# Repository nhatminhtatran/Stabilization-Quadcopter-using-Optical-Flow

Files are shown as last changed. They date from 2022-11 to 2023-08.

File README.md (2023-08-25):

<p align="center">
 <h1 align="center">Project on Robotics - Design model and PID controller for balanced Quadcopter using Optical Flow algorithm</h1>
</p>

# Introduction
This project does the following tasks:
- Build hardware for Quadcopter model with dimensions 198x235x85 mm.
- Design a PID controller to stabilize the position of the Quadcopter chassis.
- Use Optical Flow image processing to keep Quadcopter balance.
- Conduct actual operation to check the response of the controller.

# Design Quadcopter model
Quadcopter is a UAV with 4 propeller engines, which generate lift for the aircraft to take off. The direction of the quadcopter propeller along with the rotation and speed are factors that determine the aircraft's ability to fly and maneuver.

Quadcopter is a robot with 6 degrees of freedom. Therefore, in addition to translational motions in the x, y and z directions, it also moves in the roll, pitch and yaw angles.

<p align="center">
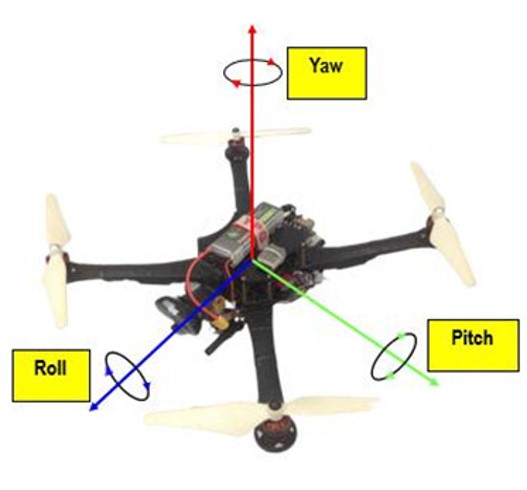
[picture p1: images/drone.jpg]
  <br/>
  <i>Movement structure of Quadcopter</i>
</p>

The model of the Quadcopter in practice after construction is as follows:

<p align="center">
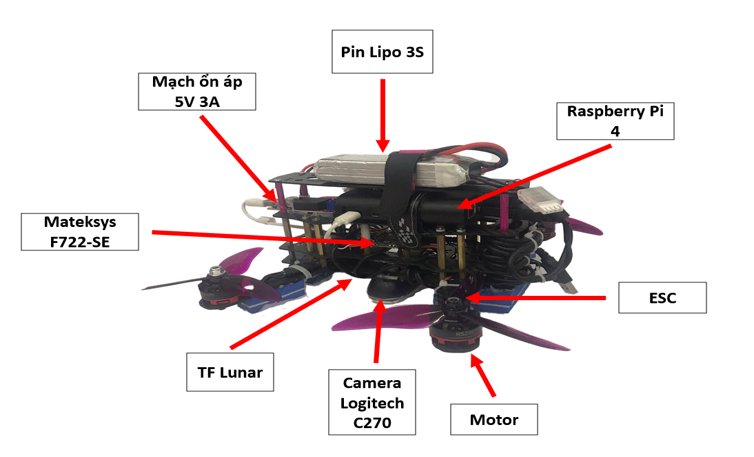
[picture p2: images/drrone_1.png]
  <br/>
  <i>Quadcopter hardware overview</i>
</p>

In this project, we use Camera Logitech C270 to apply Optical Flow to calculate drift from the Center of Frame and TF-Lunar 1D Lidar to calculate height of the Quadcopter. After that, we use that two-signal to control Quadcopter through two PID-controller. The protocol we use to control Quadcopter is YAMSPy (Yet Another Multiwii protocol).

# Optical Flow algorithm
The image processing algorithm used in the project is presented as the flowchart below:

<p align="center">
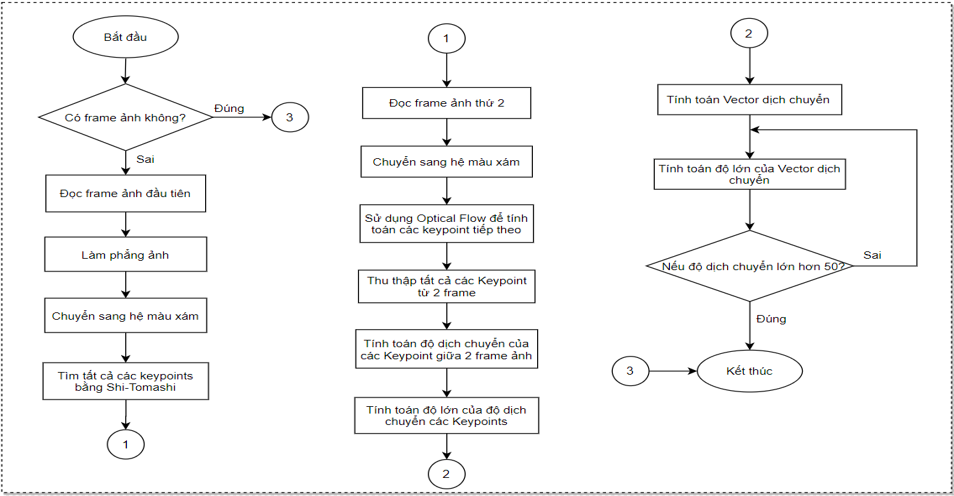
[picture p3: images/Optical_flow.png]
  <br/>
  <i>Flowchart of image processing algorithm</i>
</p>

The above diagram shows the whole process of finding the displacement vector to generate the input value for balancing. First, the camera will read the first image frame, then flatten the image from the parameters after the camera Calibration because the image retrieved from the camera will be curved so the displacement vector will be incorrect. Then convert the image frame to grayscale. Because after flattening the image, the edge of the image will appear as a cut angle, making the Harris Corner algorithm recognize it as a keypoint, which will cause errors in the vector calculation. That's why we have to cut the center part. Then, using Harris Corner algorithm to find keypoints in the image frames. Then use Optical flow algorithm to calculate the displacement between frames and get the corresponding Displacement Vector value.

<p align="center">
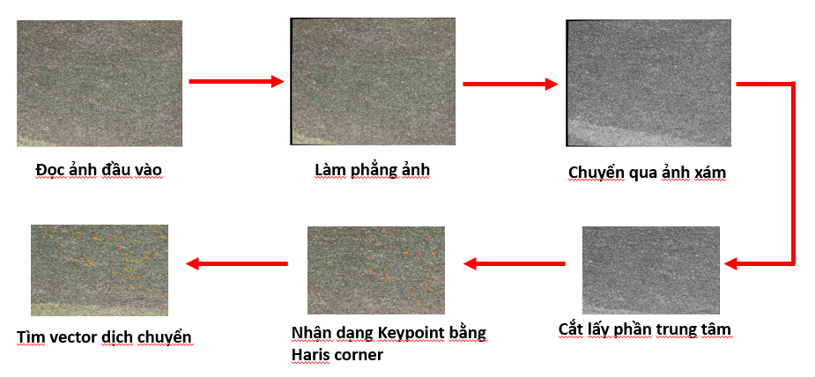
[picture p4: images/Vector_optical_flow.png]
  <br/>
  <i>Displacement Vector Calculation Process</i>
</p>

However, there are still cases that cause the process to be terminated. That is when the Quadcopter moves too far from the original point (50cm), the image processing algorithm will end. Then, Quadcopter will update the Keypoints and start the image processing again.

# Build a PID controller
The first controller is the altitude controller. In order for the Quadcopter to maintain altitude, the control signal value is the Throttle control pulse output value. In order for the Quadcopter to maintain the desired altitude, the PID controller value needs to be calibrated so that the Throttle value is calculated around the equilibrium working point.

<p align="center">
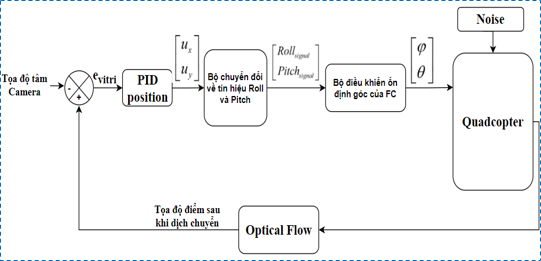
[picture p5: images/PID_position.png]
  <br/>
  <i>Block diagram of position PID controller</i>
</p>

<p align="center">
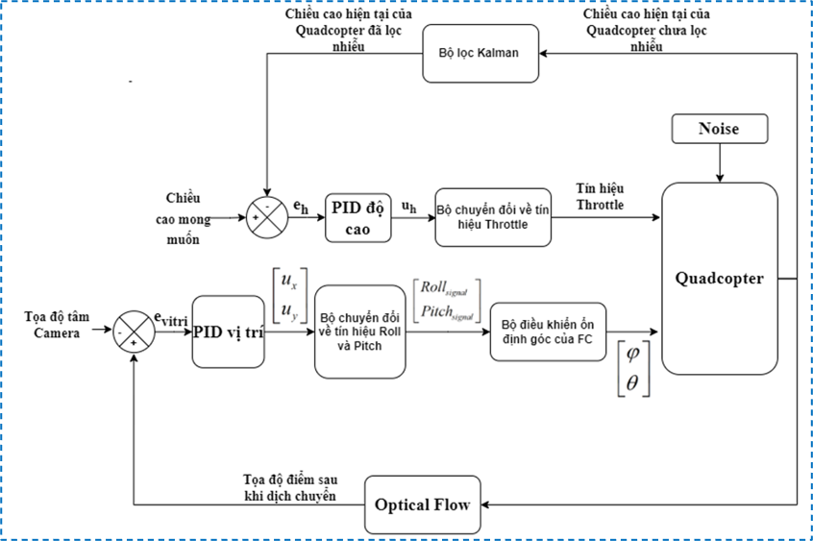
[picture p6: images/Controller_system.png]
  <br/>
  <i>General controller of the system</i>
</p>

# Results and reviews

- **Evaluation of image processing algorithms:**
Because the camera is always curved, the value of the image processing algorithm is often wrong. Therefore, the process of camera calibration plays a very important role.
<p align="center">
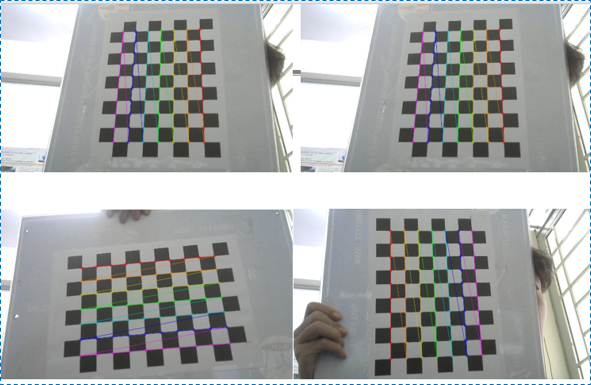
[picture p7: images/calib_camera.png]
  <br/>
  <i>Camera calibration process</i>
</p>

- **Optical Flow algorithm results:**
Result of applying PLK (Pyramid Lucas – Kanade) algorithm when there are few features (left figure).
Result of applying PLK (Pyramid Lucas – Kanade) algorithm when there are many features (right figure).

<div style="display: flex;">
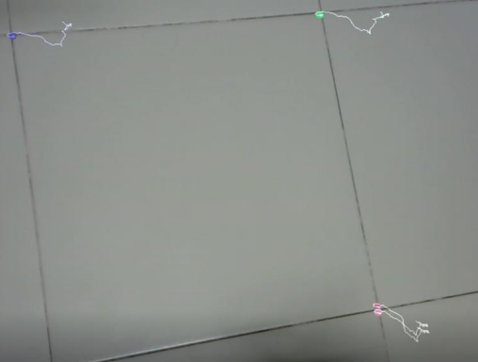
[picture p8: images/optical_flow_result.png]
  
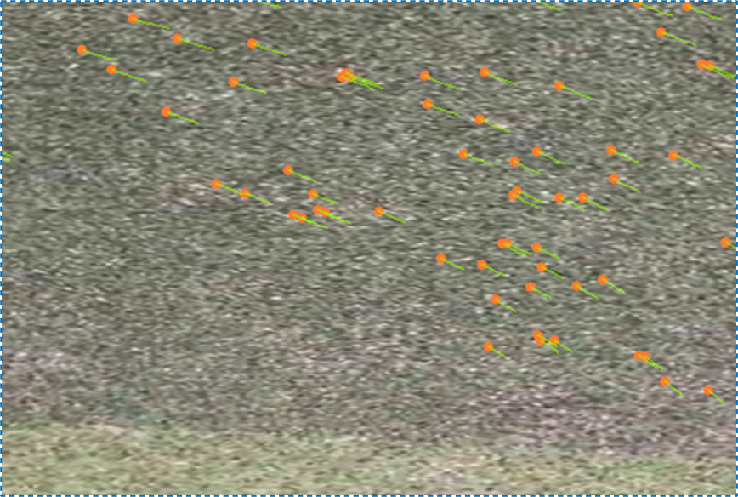
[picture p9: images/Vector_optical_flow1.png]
  
</div>

- **Evaluation of the PID controller:**
The PID controller applies to the Drone model to control altitude and position hold.

<p align="center">
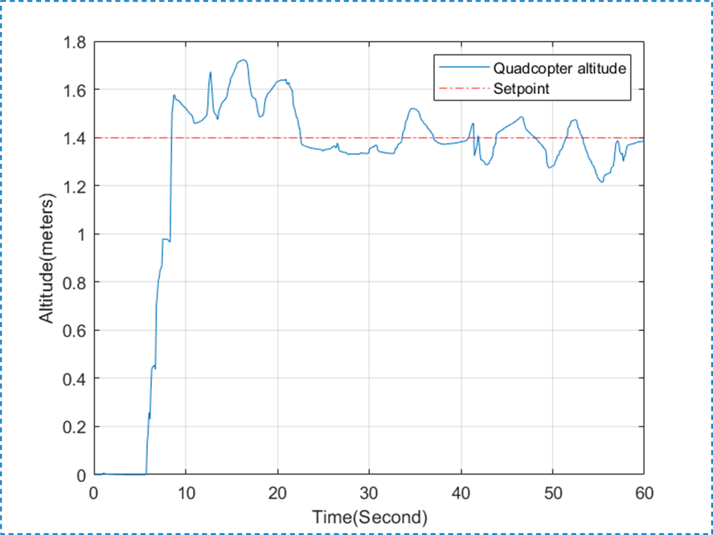
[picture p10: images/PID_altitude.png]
  <br/>
  <i>Result of PID controller holding altitude</i>
</p>

<p align="center">
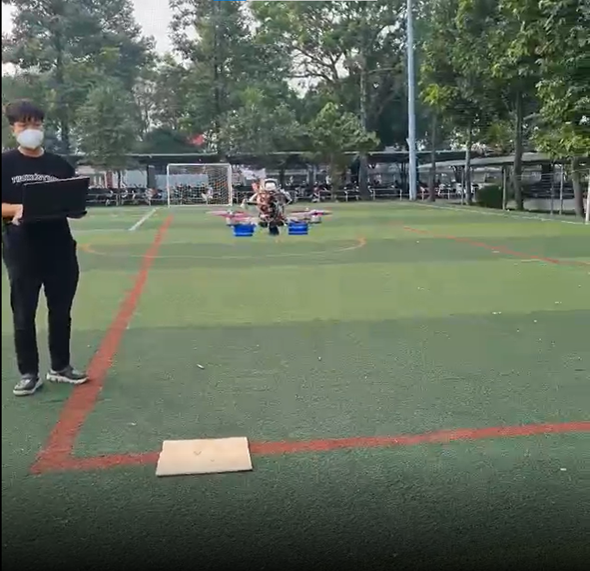
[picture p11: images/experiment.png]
  <br/>
  <i>Realistic results quadcopter keeps altitude and position</i>
</p>

# Video
https://youtu.be/sdybXYhyMzA

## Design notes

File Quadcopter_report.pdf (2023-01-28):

## BỘ GIÁO DỤC & ĐÀO TẠO

### TRƯỜNG ĐẠI HỌC SƯ PHẠM KỸ THUẬT TP. HỒ CHÍ MINH

### KHOA ĐIỆN – ĐIỆN TỬ

### BỘ MÔN TỰ ĐỘNG ĐIỀU KHIỂN

-----------------⸙∆⸙-----------------

# ĐỒ ÁN MÔN HỌC

## ĐỀ TÀI:Thiết kế mô hình và bộ điều khiển PID cho

## Quadcopter cân bằng dùng thuật toán Optical Flow

### Tp. Hồ Chí Minh tháng 1 năm 2023

### GVHD: TS. Trần Đức Thiện

SVTH: | MSSV:
Nguyễn Đức Mạnh | 19151253
Tạ Trần Nhật Minh | 19151034

## Hình ảnh đề tài

## Lời cảm ơn

Trong khoảng thời gian ba năm được học tập và rèn luyện dưới mái trường Đại học Sư phạm Kỹ thuật Tp. Hồ Chí Minh đã cho chúng em cơ hội tiếp thu những kiến

thức không chỉ có trong sách vở mà còn là những câu chuyện thực tế, những ví dụ minh

họa sinh động được các Thầy, Cô truyền đạt vào những buổi học lý thuyết và thực hành,

tất cả sẽ là hành trang tri thức quý báu, là nền tảng vững vàng nâng bước chúng em trên

con đường sự nghiệp phía trước.
Nhóm em xin được gửi lời cảm ơn chân thành đến thầy TS. Trần Đức Thiện đã tận

tình chỉ bảo, hướng dẫn và đóng góp những ý kiến vô cùng quý giá giúp nhóm em hoàn

thành đồ án môn học này. Nhóm cũng xin cám ơn quý Thầy, Cô đang công tác tại khoa

Điện - Điện tử cùng các Thầy, Cô trong toàn trường đã giảng dạy nhiệt tình và truyền

tải các kinh nghiệm quý giá cho nhóm trong suốt ba năm học vừa qua.

Tuy đã có sự chuẩn bị trong bài báo cáo đồ án môn học này song không thể tránh

khỏi những sai sót. Vì vậy, nhóm em rất mong nhận được sự chỉ bảo, đóng góp ý kiến

của quý Thầy Cô để nhóm có cơ hội nâng cao kiến thức và kĩ năng của mình, cũng như

là một nền tảng vững chắc để nhóm tiến xa hơn trong tương lai.

Nhóm em xin chân thành cảm ơn!

## Mục lục

Mục lục

## Danh sách hình ảnh

## Danh sách bảng

CHƯƠNG 1. TỔNG QUAN

BỘ MÔN ĐIỀU KHIỂN TỰ ĐỘNG | 1

## Chương 1. TỔNG QUAN

### 1.1 GIỚI THIỆU

Trong những năm gần đây, với sự phát triển của công nghệ 4.0, UAV (Unmanned

Arial Vehicle) ngày càng phổ biến và được sử dụng rộng rãi trong nhiều lĩnh vực trong

cuộc sống, từ trong nông nghiệp cho đến quân sự. UAV được định nghĩa là phương tiện

cơ giới không có người lái, sử dụng lực khí động học để di chuyển. UAV có thể bay

thông qua tín hiệu điều khiển bằng tay cầm hoặc tự hành bằng các hệ thống máy tính

nhúng xử lý chương trình điều khiển. Các quốc gia phát triển như Mỹ, Nga, Trung Quốc

đều đang đẩy mạnh phát triển các hệ thống máy bay không người lái vào trong lĩnh vực

quân sự. Ngoài ra, các biến thể của UAV còn được sử dụng rộng rãi trong tìm kiếm cứu

hộ, khai thác những nơi mà con người không thể đặt chân đến được, hay áp dụng trong

việc giao hàng, quay phim...
Quadcopter là một dạng phổ biến nhất của UAV được trang bị với bốn động cơ và

bốn cánh quạt, hoạt động dựa trên nguyên lý động học. Quadcopter bắt đầu định hình

được cấu trúc máy bay vào đầu những năm thập niên 2000s. Mãi cho đến giai đoạn từ

2005-2010, với sự ra đời của nhiều vi điều khiển và cảm biến có kích thước và khối

lượng nhỏ như IMU, Barometer, đã tạo điều kiện cho sự phát triển bùng nổ của

Quadcopter với khả năng giao tiếp đa dạng và dễ dàng thiết kế nhỏ gọn hơn trước. Chính

vì sự đa di năng của các hệ thống quadcopter, ngày nay nhiều thuật toán điều khiển

thông minh như xử lý ảnh hay trí tuệ nhân tạo ngày càng được áp dụng nhiều trên các

mô hình quadcopter này. Do đó tình hình nghiên cứu về drone ngày càng được mở rộng

và phát triển cả trên thị trường quốc tế và trong nước.

### 1.1.1 Nghiên cứu quốc tế

Trong những năm gần đây, thị trường thương mại của drone đang ngày càng phát

triển mạnh mẽ. Mặc dù sự ra đời của Covid-19 đã tác động nghiêm trọng đến nhu cầu

sử dụng và chế tạo máy bay không người lái, việc kết nối lại các hoạt động kinh tế vào

năm 2021 đã phục hồi nhu cầu về máy bay không người lái. Máy bay không người lái

đã định nghĩa lại và nâng cao năng suất của nhiều ngành. Với sự tăng trưởng trong việc

ứng dụng drone trong các lĩnh vực khác nhau, các công ty đang đầu tư đáng kể vào các

CHƯƠNG 1. TỔNG QUAN

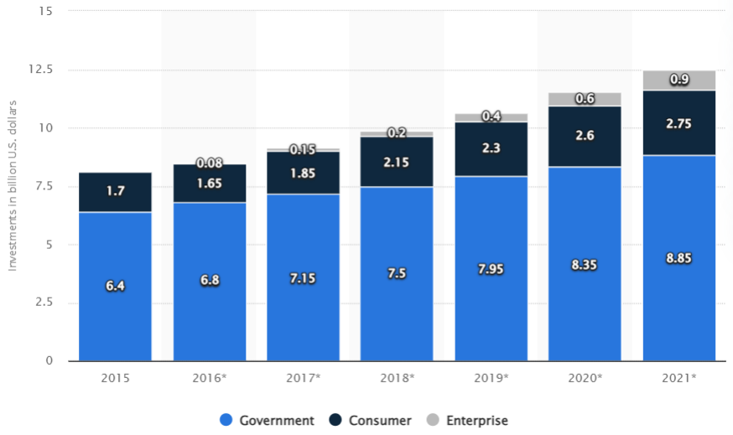
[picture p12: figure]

BỘ MÔN ĐIỀU KHIỂN TỰ ĐỘNG | 2

giải pháp phân tích chế tạo máy bay không người lái. Trong đó DJI là hãng sản suất

drone lớn nhất thế giới có trụ sở tại Trung Quốc và nơi đây đã trở thành trung tâm sản

xuất máy bay không người lái toàn cầu trong sáu năm qua. Hãng nghiên cứu thị trường

BI Intelligence đã đưa ra ước tính đầu tư phần cứng của drone trên thị trường toàn cầu

đạt hơn 12 tỷ USD vào năm 2021.

Hình 1.1: Thị phần đầu tư vào lĩnh vực drone tính đến năm 2021

Hình 1.2: DJI Mavic Pro Mini

Flycam
Flycam là thiết bị bay không người lái được trang bị camera cho phép người dùng

điều khiển, quan sát từ xa để chụp ảnh và ghi hình trên cao. Hiện nay thiết bị này chắc

hẳn không còn xa lạ với mọi người. Flycam ngày càng được đổi mới về kiểu dáng, kích

thước, thời gian bay, khoảng cách điều khiển, chất lượng camera, công nghệ và giá cả

hợp lý. Hình dưới đây cho thấy hình ảnh một chiếc Flycam khá phổ biến trên thị trường

– DJI Mavic 3.

CHƯƠNG 1. TỔNG QUAN

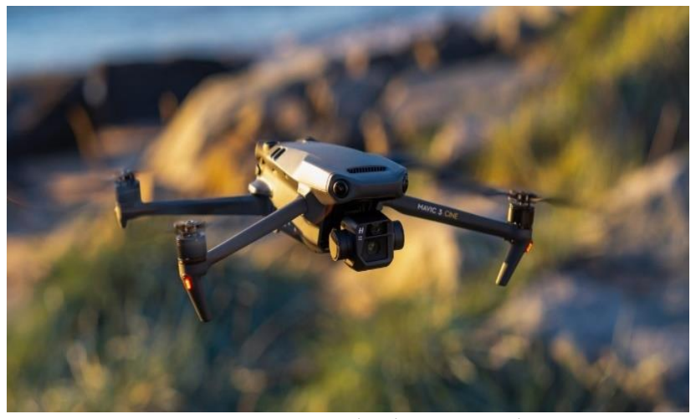
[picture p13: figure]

BỘ MÔN ĐIỀU KHIỂN TỰ ĐỘNG | 3

Hình 1.3: Một mô hình DJI Mavic 3

Drone với công nghệ theo dõi đối tượng và tránh vật cản

Với công nghệ theo dõi đối tượng, drones được lập trình để bay bám theo đối

tượng, mang đến những thước phim độc đáo. Với DJI Mavic3, hãng có sử dụng công

nghệ Active Track, người dùng có thể chọn bounding box bao quanh đối tượng cần

Track và drone sẽ bay bám theo đối tượng đó. Tính năng Follow-me cũng giúp drone

bay theo người khi chỉ có một người trong khung hình bằng cách sử dụng GPS. Bên

cạnh đó, việc trang bị các cảm biến Lidar giúp drone có thể tránh vật cản trong quá trình

bay.

Hình 1.4: Drone bay bám theo đối tượng

Máy bay không người lái sử dụng GPS/GCS
Máy bay không người lái trang bị GPS, được điều khiển từ xa thông qua các thiết

bị như điện thoại, máy tính bảng hoặc máy tính cùng với một máy phát sóng radio telemetry được gọi là trạm điều khiển mặt đất (GCS). Từ trạm điều khiển mặt đất, máy

bay có thể được điều khiển theo một lộ trình được quy hoạch sẵn. Ngoài ra, máy bay

không người lái có thể được lập trình để theo dõi máy phát có trang bị GPS để giữ đối

tượng trong khung hình máy ảnh. Việc theo dõi đối tương sử dụng GPS cũng là một

CHƯƠNG 1. TỔNG QUAN

BỘ MÔN ĐIỀU KHIỂN TỰ ĐỘNG | 4

hướng nghiên cứu và đã có sản phầm thương mại. Tuy nhiên GPS cũng có nhược điểm

là dễ bị nhiễu sóng và mất tín hiệu ở một số nơi địa hình rừng núi hiểm trở.

Drone trình diễn ánh sáng

Drone ngày nay còn được ứng dụng trong các dự án trình diễn ánh sáng cho các

sự kiện lớn. Dự án trình diễn ánh sáng bằng drone đạt kỷ lục Guinness của hãng xe hơi

Genesis Trung Quốc với 3281 drones.

Hình 1.5: Drone trình diễn ánh sáng

### 1.1.2 Nghiên cứu trong nước

Nghiên cứu của sinh viên trong nước
Chủ đề drone là một chủ đề khá hấp dẫn và thu hút nhiều bạn sinh viên đam mê

nghiên cứu. Nhiều mô hình drone đã được chọn để nghiên cứu trong các luận văn đồ án

tốt nghiệp cũng như nghiên cứu khoa học. Tuy nhiên yêu cầu nhiều về kiến thức khoa

học và việc thiếu kinh nghiệm nghiên cứu UAV, nên các đề tài về máy bay không người

lái của sinh viên vẫn còn nhiều hạn chế. Máy bay không người lái kết hợp với các công

nghệ mới như xử lý ảnh, thuật toán AI, IoT,… đã và đang được nghiên cứu và giảng dạy ngày càng nhiều tại các trường đại học.

Tình hình nghiên cứu một số đề tài tiêu biểu về drone của trường đại học Sư Phạm

Kỹ thuật TP.Hồ Chí Minh được trình bày như bảng 1:

CHƯƠNG 1. TỔNG QUAN

BỘ MÔN ĐIỀU KHIỂN TỰ ĐỘNG | 5

Bảng 1: Các đề tài nghiên cứu về drone ở trường đại học Sư phạm Kỹ thuật TP. HCM

STT | Tên đề tài | Tác giả | Khóa | Nội dung
1 | Design and implement a quadcopter model autonomuosly landing on a stationary target | Trần Lê Anh, Lê Tuấn Thông | K14 | Thiết kế và sử dụng các bộ điều khiển PID, LQR, bộ lọc Kalman và giải thuật xử lý ảnh để quadcopter tự động hạ cánh trên một vị trí xác định.
2 | Research, design and construct an autonomuos human detection and tracking quadcopter prototype | Lê Mạnh Cường | K15 | Nghiên cứu, thiết kế và ứng dụng bộ điều khiển PID, mạng học sâu SSD MobileNet v2-lite và thuật toán tracking để quadcopter tự động phát hiện và bám theo người.
3 | Xây dựng mô hình quadcopter và điều khiển bay bám theo đối tượng | Nguyễn Văn Minh Phụng, Nguyễn Thành Quang | K16 | Nghiên cứu, thiết kế và ứng dụng bộ điều khiển PID và giải thuật xử lý ảnh để drone bay bám theo một vật thể di động.
4 | Nghiên cứu, thiết kế và chế tạo mô hình quadcopter tự hành bay qua khoảng trống hẹp | Lê Ngọc Hiền Đức | K17 | Nghiên cứu, thiết kế và chế tạo mô hình quadcopter; sử dụng giải thuật xử lý ảnh và tính toán quỹ đạo để quadcopter bay qua một khoảng trống hẹp.
5 | Điều khiển mô hình drone bay bám theo đối tượng | Trương Lê Anh Tiến | K18 | Nghiên cứu, áp dụng giải thuật thị giác máy và mô hình mạng học sâu để điều khiển drone bay bám theo đối tượng.

Nghiên cứu máy bay không người lái
Về lĩnh vực này nước ta cũng đạt được một số thành tựu nhất định. Có nhiều trung

tâm, công ty nghiên cứu về UAV đã đạt được nhiều kết quả rất khả quan. Các mô hình

đã đáp ứng được nhu cầu thực tế được đặt ra, đáp ứng được yêu cầu trong nước lẫn quốc

tế. Đi đầu trong lĩnh vực này là các trung tâm nghiên cứu của Bộ quốc phòng với nhiều

loại máy bay không người lái thực hiện các nhiệm vụ quân sự, nghiên cứu, giám sát trên không và cứu hộ cứu nạn. Bên cạnh đó cũng có nhiều công ty sản xuất và cung cấp giải

pháp về drone, ứng dụng chủ yếu trong các lĩnh vực nông nghiệp, công nghiệp và đã

xuất khẩu sang các thị trường Mỹ, Châu Âu, Ấn Độ, …. Hình dưới đây là mô hình

CHƯƠNG 1. TỔNG QUAN

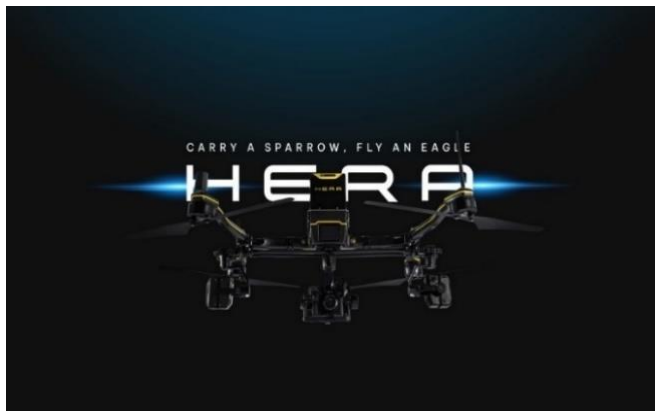
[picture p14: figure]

BỘ MÔN ĐIỀU KHIỂN TỰ ĐỘNG | 6

HERA Drone mới nhất của Công ty TNHH Real-time Robotics Việt Nam được đem đi

triển lãm tại Mỹ, là niềm tự hào của ngành công nghiệp Drone Việt Nam.

Hình 1.6: HERA Drone

Quadcopters có các đặc điểm thuận lợi cho nhiều ứng dụng như kiểm tra cơ sở hạ

tầng, theo dõi và giám sát tài sản, do khả năng di chuyển qua lại, cất cánh và hạ cánh

thẳng đứng. Nhờ sự phát triển gần đây của các thuật toán điều khiển máy bay, khả năng

xử lý hình ảnh và đặc biệt là học máy, các máy bay quadcopters giờ đây có cơ hội tự chủ và được thông qua để cung cấp các chức năng trong nhiều kịch bản ứng dụng. Tuy

nhiên, nó cần được thiết kế một bộ điều khiển tốt để có thể giữ ổn định độ cao và cân

bằng khi thực hiện hành trình bay. Để thực hiện nhiệm vụ điều khiển ổn định đòi hỏi độ

khó cao, vì Quadcopter là một robot với sáu bậc tự do nhưng chỉ có 4 giá trị ngõ vào điều khiển. Vì vậy, mục tiêu đồ án này là phát triển bộ điều khiển để giúp Quadcopter

bay ổn định hơn.

### 1.2 MỤC TIÊU ĐỀ TÀI

Xây dựng phần cứng cho mô hình Quadcopter với kích thước

198 235 85 mm 10% × | × | ± | .
Thiết kế bộ điều khiển PID để ổn định vị trí cho bộ khung Quadcopter bằng cách

kết hợp cảm biến khoảng cách và xử lý ảnh.

Sử dụng xử lý ảnh dùng Optical Flow để giữ cân bằng Quadcopter. Dựa trên cảm

biến TF Lunar 1D Lidar để đọc độ cao của Quadcoper, IMU cung cấp thông tin về độ

nghiêng và góc quay để giúp cho quá trình cân bằng được ổn định hơn.

Tiến hành vận hành thực tế để kiểm tra đáp ứng của bộ điều khiển.

CHƯƠNG 1. TỔNG QUAN

BỘ MÔN ĐIỀU KHIỂN TỰ ĐỘNG | 7

### 1.3 PHƯƠNG PHÁP NGHIÊN CỨU

Đọc các bài báo khoa học nước ngoài và trong nước liên quan đến phạm vi nghiên

cứu hoặc đối tượng liên quan, các tài liệu tham khảo, trao đổi với các anh/chị và thầy/cô

đã từng làm các đề tài có liên quan đến.

Phương pháp nghiên cứu cho đối tượng drone là áp dụng phương pháp thử sai các

thông số của bộ điều khiển PID để tìm ra bộ thông số tốt nhất.

### 1.4 NỘI DUNG

Chương 1: Tổng quan

Chương này trình bày một cách tổng quan về đồ án thực hiện bao gồm giới thiệu

đề tài, mục tiêu đề tài, phương pháp nghiên cứu và nội dung đề tài.

Chương 2: Cơ sở lý thuyết

Chương này cung cấp cơ sở lý thuyết phục vụ cho đồ án gồm lý thuyết điều khiển

máy bay, lý thuyết động học và mô hình toán học, bộ điều khiển PID và xử lý ảnh dùng

Optical Flow.
Chương 3: Thiết kế hệ thống

Chương này trình bày chi tiết về thiết kế phần cứng của mô hình, bao gồm phần

khung và các thiết bị điện tử ở trên máy bay. Hệ thống cơ khí gồm hình dáng, kích thước

và lắp ráp các bộ phận máy bay.

Chương 4: Thuật toán điều khiển

Chương này trình bày chi tiết về cách thiết kế thuật toán cho bộ điều khiển PID

của máy bay và áp dụng thuật toán Optical Flow cho Quadcopter cân bằng.

Chương 5: Kết quả và đánh giá

Chương này trình bày chi tiết kết quả thực nghiệm khi ứng dụng bộ điều khiển PID

trên mô hình Quadcopter, đánh giá về độ ổn định của Quadcopter khi dùng xử lý ảnh.

CHƯƠNG 2. CƠ SỞ LÝ THUYẾT

BỘ MÔN ĐIỀU KHIỂN TỰ ĐỘNG | 8

## Chương 2. CƠ SỞ LÝ THUYẾT

### 2.1 LÝ THUYẾT ĐIỀU KHIỂN MÁY BAY

UAV rất đa dạng về các biến thể, tùy thuộc vào số cánh quạt mà có thể đặt tên cho

từng loại. Quadcopter là một UAV với 4 động cơ cánh quạt, tạo ra lực nâng để máy bay

cất cánh. Hướng của cánh quạt quadcopter cùng với vòng quay và tốc độ là các yếu tố

quyết định khả năng bay và cơ động của máy bay.

Để máy bay có thể cất cánh bay lên không trung, một lực tạo ra phải có độ lớn lớn

hơn lực hấp dẫn của trái đất. Khi bay lên, các cánh quạt quadcopter đẩy không khí xuống

và tạo ra lực nâng nâng thân máy bay lên. Tất cả 4 cánh quạt phải tạo ra lực đẩy bằng

nhau khi quadcopter cất cánh và hạ cánh (tăng hoặc giảm ga). Quadcopter là một robot

với 6 bậc tự do. Chính vì vậy, ngoài các chuyển động tịnh tiến theo các phương x, y và

z, nó còn chuyển động theo các góc roll, pitch và yaw. Yaw là độ lệch hoặc quay đầu

hoặc sang phải hoặc trái của quadcopter. Góc yaw được điều khiển bằng cách thay đổi

tốc độ giữa các cặp động cơ trước - phải sau – trái và trước – trái sau – phải sao cho tổng

lực đẩy của bốn rotor là không đổi. Pitch là chuyển động của quadcopter về phía trước

hoặc phía sau. Góc pitch được điều khiển bằng cách thay đổi tốc độ của phía trước (cánh

quạt trước bên phải - trục trước) và phía sau (cánh quạt sau phải - sau trái), trong khi vẫn giữ được tổng lực đẩy. Roll là góc mà thể hiện độ nghiêng về một bên, ví dụ như

nghiêng sang trái hoặc phải). Góc roll được điều khiển bằng cách thay đổi tốc độ giữa

bên phải (cánh quạt trước-phải và cánh quạt sau-phải) và bên trái (cánh quạt trước trái

và cánh quạt sau trái).

CHƯƠNG 2. CƠ SỞ LÝ THUYẾT

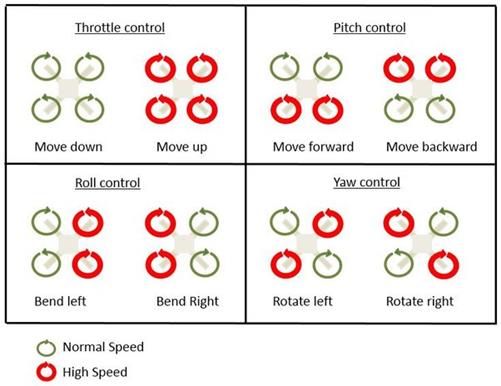
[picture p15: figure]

BỘ MÔN ĐIỀU KHIỂN TỰ ĐỘNG | 9

Hình 2.1: Cấu trúc chuyển động của Quadcopter

Hình 2.2: Các chuyển động cơ bản của Quadcopter

### 2.2 LÝ THUYẾT ĐỘNG HỌC VÀ MÔ HÌNH TOÁN HỌC

### 2.2.1 Lý thuyết động học

Một quadcopter có cấu trúc động học được trình bày ở Hình 2.3 với tốc độ góc,

momen quán tính và lực nâng được điều khiển bằng bởi bốn động cơ cánh quạt.

CHƯƠNG 2. CƠ SỞ LÝ THUYẾT

BỘ MÔN ĐIỀU KHIỂN TỰ ĐỘNG | 10

Hình 2.3: Các giá trị biến động học trên Quadcopter

Các vị trí tuyến tính tuyệt đối được xác đinh trong khung quán tính theo trục x,y,z

là ξ. Độ cao phụ thuộc vào các vị trí góc, với các đại lượng được xác định theo ba góc

Euler η là roll, pitch và yaw. Góc pitch θ mô tả cho sự quay của thân máy bay quanh trục y. Góc roll ϕ thể hiện sự quay quanh trục x và góc yaw ψ xung quanh trục z. Vector

q là một ma trận chứa cả hai vector vị trí dịch chuyển tuyến tính ξ và vector vị trí góc η.

x
y , | ,q
z
é ù | é ù φ
éù ξ ê ú | ê ú ξ = | η = θ | = êú ê ú | ê ú | ëû η
ê ú | ê ú ë û | ë û ψ

(1.1)

Gốc tọa độ đặt trục của khung máy bay là ở giữa khung máy bay. Từ gốc tọa độ,

ta định nghĩa được các ma trận vận tốc tuyến tính VB và vận tốc góc v.

x,B

B | y,B
| z,B
| v | | p
V | v | , v | q
| v | | r
é | ù | éù ê | ú | êú
= | = ê | ú | êú ê | ú | êú ë | û | ëû

(1.2)

Ma trận xoay từ khung mô hình đến khung quán tính là:

C C | C S S | S C | S C | S S S
R | S C | S | C C | S | C | C C S S | S
S | C S | C C
ψ | θ | ψ θ φ | ψ | φ | ψ | ψ φ θφ
ψ | θ | ψ | ψ | φ | ψ | ψ | φ θ φ | θ | φ
θ | θ φ | θ | φ
é | ù − | − ê | ú
= | − | − ê | ú
ê | ú − ë | û

(1.3)

Trong đó:

( ) ( )
1
cos | , | sin | , | T C | x S | x R | R x | x
−
= | = | =
là ma trận nghịch đảo thực hiện phép

xoay từ hệ quán tính đến khung mô hình.

CHƯƠNG 2. CƠ SỞ LÝ THUYẾT

BỘ MÔN ĐIỀU KHIỂN TỰ ĐỘNG | 11

Ma trận chuyển đổi cho vận tốc góc từ hệ tuyến tính đến hệ trục thân máy bay là

Wη

. Và ma trận nghịch đảo

1 W⁻
η

thể hiện sự chuyển đổi từ hệ trục thân máy bay sang hệ

tuyến tính.

Wv¹

1 | S T | C T | p
0 | C | S | q
0 S / C | C / C | r

−
η
φ θ | φ θ
φ | φ
φ | θ | φ | θ

η=
éù φ | é | ùéù êú ê | úêú θ = | − êú ê | úêú êú ψ | ê | úêú ëû ë | ûëû
(1.4)

vW

p | 1 | 0 | S
q | 0 | C | C S
r | 0 | S | C C

η

θ

φ | θ φ
θ | θ | φ
= | η
éù é | ù − | φéù
êú ê | úêú = | θ êú ê | úêú
êú ê | ú − | ψêú ëû ë | ûëû

(1.5)

Trong đó:
T | x x

= tan ( ) , Ma trận
Wη

có thể nghịch đảo nếu

2 1
,
2

k

θ | φ kZ æ | ö −
≠ | Î ç | ÷ è | ø

Cấu trúc của quadcopter là đối xứng nên ma trận quán tính là một ma trận chéo Y

trong đó giá trị
xx | yy
I | I = | .

xx

yy

zz

| I | 0 | 0
I | 0 | I | 0
| 0 | 0 | I
é | | ù
ê | | ú
=
ê | | ú
ê | ú ë | û

(1.6)

Vận tốc góc của rotor I, được kí hiệu là ωi
, sẽ tạo ra một lực
i

f

theo hướng trục

của rotor. Vận tốc góc và gia tốc của rotor cũng sinh ra momen

Mi

τ

xung quanh trục

động cơ.

i

2 | 2
i | M | M | i f | k , | b | I = ω τ = ω + ω
(1.7)

Trong đó:

k

là hệ số nâng,
b

là hệ số cản,
M

I
là momen quán tính của rotor.

Lực tổng hợp của các rotor tạo ra lực đẩy T theo hướng của trục Z của khung mô

hình.

B
T
là lực tác dụng lên khung mô hình. Momen
B

τ
bao gồm các momen
φ

τ θ

τ
và

ψ

τ
theo các hướng của các góc trong khung mô hình tương ứng.

CHƯƠNG 2. CƠ SỞ LÝ THUYẾT

BỘ MÔN ĐIỀU KHIỂN TỰ ĐỘNG | 12
4 | 4
| 2
i | i
i 1 | i 1

B

T | f | k
| 0
T | 0
| T
= | =
= | = | ω

éù
êú
=
êú

### êú ëû

∑ ∑

(1.8)

i

| 2 | 2 | 2 | 2
| 4 | 3 | 2 | 1
| 2 | 2 | 2 | 2
B | 4 | 3 | 2 | 1
4

M
| | i1
lk( | )
lk( | )

φ

θ

ψ

=

é | ù
ê | ú éù τ | ω + ω − ω − ω ê | ú êú
τ = τ | = | ω − ω − ω + ω ê | ú êú ê | ú êú τ
ëû ê | ú τ
ê | ú ë | û ∑

(1.9)

Trong đó:
l
là khoảng cách giữa động cơ và trọng tâm của quadcopter.
Chuyển động của trục Roll có được bằng cách giảm vận tốc rotor thứ hai và thứ

nhất và ngược lại ta tăng vận tốc với rotor thứ ba và thứ tư.

Chuyển động của trục Pitch có được bằng cách giảm vận tốc rotor thứ nhất và thứ

tư cùng đó tăng vận tốc của rotor thứ hai và thứ hai.

Chuyển động của trục Yaw có được bằng cách tăng tốc độ của hai rotor quay ngược

chiều nhau và giảm của hai rotor ngược lại.

### 2.2.2 Phương trình Newton-Euler

Quadcopter được giả định là một vật cứng, do đó để mô tả động học của nó thì có

thể sử dụng phương trình Newton-Euler. Trong hệ trục khung máy bay, tổng lực cần

thiết cho gia tốc của khối lượng
mVB

và lực ly tâm

v | mV ×( | B )

bằng với tổng của trọng

lực

T RG
và lực đẩy đẩy của rotor
TB
T mV | v (mV ) | R G T B | B | B + × | = | +
(1.10)

Trong khung quán tính, lực ly tâm bị vô hiệu hóa. Do đó, chỉ có lực hấp đẫn lực,

độ lớn và hướng của lực đẩy đóng góp vào gia tốc của quadcopter.

m | G | RT ξ = | + | B

(1.11)

x | 0 | C S C | S S
T
y | g 0 | S S C | C S
m
z | 1 | C C
ψ θ | φ | ψ φ
φ θ | φ | ψ φ
θ | φ
é ù | é ù | é | ù +
ê ú | ê ú | ê | ú
= − | + | − ê ú | ê ú | ê | ú
ê ú | ê ú | ê | ú ë û | ë û | ë | û

(1.12)

CHƯƠNG 2. CƠ SỞ LÝ THUYẾT

BỘ MÔN ĐIỀU KHIỂN TỰ ĐỘNG | 13

Trong khung mô hình, gia tốc góc của quán tính Iv

, lực hướng tâm

v (Iv) ×
và lực

con quay (gyroscoper)
Γ

bằng momen ngoài
τ.
τ = | + × | + Γ Iv v (Iv)
(1.13)

zz
1
yy | r

xx

| p | I p | p | 0
v I ( | q | I p | I q | 0 | )
| r | I p | r | 1

−
Γ
é ù é | ù | é ù é ù
ê ú ê | ú | ê ú ê ú = | − | × | − | × | ω + τ ê ú ê | ú | ê ú ê ú
ê ú ê | ú | ê ú ê ú ë û ë | û | ë û ë û

(1.14)

yy | zz | xx | | xx | xx
zz | xx | yy | r | yy | yy
xx | yy | zz | | | zz
p | (I | I )qr / I | | q / I | / I
q | (I | I )qr / I | I | q / I | / I
r | (I | I )qr / I | | 0 | / I

φ

Γ | θ

ψ

é ù | é | ù é | ù − | τé | ù
ê ú | ê | ú ê | ú | ê | ú
= | − | − | − | ω + τ ê ú | ê | ú ê | ú | ê | ú
ê ú | ê | ú ê | ú − | τê | ú ë û | ë | û ë | û | ë | û

(1.15)

Trong đó:
ω ω ω ω ω Γ = | − | + | − 1 | 2 | 3 | 4

là gia tốc góc trong khung quán tính bị ảnh

hưởng bởi gia tốc trong khung mô hình với ma trận biến đổi

1 W⁻
η

và đạo hàm theo thời

(1.16)

### 2.2.3 Hiệu ứng khí động học

Ở những phần trên, mô hình toán học được xây dựng trong điều kiện không có sự

tác động từ những yếu tố ngoại lực phức tạp. Thực tế, mô hình Quadcopter khi thực

nghiệm sẽ phải chịu thêm lực cản do không khí tạo ra và điều này ảnh hưởng đến sự vận

hành ổn định của mô hình. Chính vì vậy, công thức sau thể hiện sự biến đổi trong gia

tốc khi có tác động của ngoại lực.

(1.17)

Trong đó:
A ,Ax y

và

Az

là các hệ số lực cản đối với vận tốc trong các hướng tương

ứng trong hệ quy chiếu quán tính.

CHƯƠNG 2. CƠ SỞ LÝ THUYẾT

BỘ MÔN ĐIỀU KHIỂN TỰ ĐỘNG | 14

Một số hiệu ứng khí động học khác có thể đưa vào mô hình. Sự ảnh hưởng của khí

động học rất phức tạp để mô hình hóa. Cũng vì thế một số các tác động lớn khi vận tốc

của mô hình đang lớn. Do đó, những hiệu ứng này sẽ được loại bỏ khỏi mô hình sẽ giúp

mô hình toán đơn giản hơn.

### 2.2.4 Hệ thống IMU

Inertial Measurement Unit (IMU) là một thiết bị đo lường điện tử nhằm xác định

các giá trị vận tốc, hướng, gia tốc trọng trường của một số phương tiện như máy bay,

tên lửa … IMU là sự kết hợp của các cảm biến bao gồm gia tốc kế, con quay hồi chuyển

và cảm biến từ tính tùy theo thiết bị. IMU thường được sử dụng để điều khiển chuyển

động của các phương tiện có người lái hoặc tự lái.
Inertial Navigation System (INS) được sử dụng hầu hết trong vận chuyển, hàng

không vũ trụ, xe cộ, cũng như robot tự động. Dữ liệu được thu thập từ các cảm biến cho

phép máy tính xác định vị trí của các đối tượng sử dụng bằng cách sử dụng cách tính

toán dẫn dường dự đoán. INS bao gồm hai thành phần: IMU và máy tính dẫn hướng.

+ IMU chịu trách nhiệm đọc các giá trị đo được từ các cảm biến (gia tốc kế, con

quay hồi chuyển …) sau đó dữ liệu sẽ được gửi đến máy tính để tính toán và xác định

vị trí hiện tại dựa trên vận tốc và thời gian.

+ Máy tính dẫn đường có nhiệm vụ chuyển đổi tọa độ, tính toán gia tốc trọng

trường và thức hiện các thuật toán tích phân. Hình 2.1 cho thấy các góc Euler của

quadcopter.
Tuy nhiên, nhược điểm cơ bản nhất của IMU là chúng thường tích lũy sai số theo

thời gian. Vì liên tục cập nhật các thay đổi được đo lường dựa trên các giá trị đã tính

toán trước đó, bất kỳ sai số nào dù là nhỏ nhất quy mô đo lường sẽ tích lũy theo thời

gian. Điều này dẫn đến sự chênh lệch giữa các giá trị tính toán và giá trị thực tế của hệ

thống. Để đảm bảo rằng độ chính xác của điều hướng hệ thống được duy trì, giải pháp

là sử đụng các module điển hình khác như Global Positioning System (GPS), cảm biến

trọng lực, cảm biến vận tốc, la bàn điện tử … các giá trị trả về trên sẽ chịu trách nhiệm

chỉnh sửa lại các giá trị IMU.

CHƯƠNG 2. CƠ SỞ LÝ THUYẾT

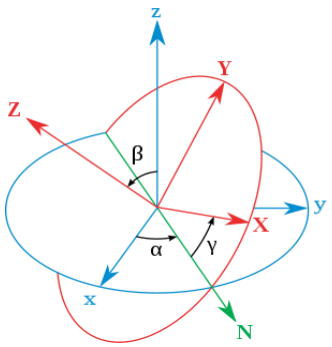
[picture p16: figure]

BỘ MÔN ĐIỀU KHIỂN TỰ ĐỘNG | 15

### 2.2.5 Xác định góc nghiêng trong không gian

2.2.5.1 Phương pháp Euler
Các góc Euler được phát triển bởi Leonhard Euler để mô tả hướng của một vật thể

khối trong không gian Euclidean ba chiều. Để cung cấp cho một đối tượng cụ thể định

hướng trong không gian nên nó được thể hiện bởi ba phép tính được mô tả bởi các

phương trình Euler cho các góc. Điều này tương đương với việc nói rằng một ma trận

xoay có thể phân tách thành một tích của ba phép quay. Leonhard Euler là người đầu

tiên cố gắng mô tả định hướng. Anh ta tưởng tượng ra ba hệ quy chiếu có thể quay ngược

nhau và nhận ra rằng bằng cách sử dụng một hệ quy chiếu cố định và thực hiện ba lần,

anh ta mô tả bất kỳ hệ quy chiếu nào trong không gian (sử dụng hai vòng quay trên một

trục tung và chuyển động quay trên hai trục còn lại). Các giá trị ba vòng quay được gọi

là góc Euler. Hình 2.4 cho thấy các góc Euler.

Một định nghĩ trước đây được gọi là quy ước z-x-z là định nghĩa thông thường nhất. Hệ thống xyz (cố định) được hiển thị bằng màu xanh lam, hệ thống XYZ (xoay)

được hiển thị bằng màu đỏ. Dòng của các nút giao của mặt phẳng tọa độ (x,y) và (X,Y)

ở mặt phẳng (N) được hiển thị màu xanh lá cây.
α

là góc giữa trục x và đường thẳng

của các nút,

β
là góc giữa trục z và trục Z, γ

là góc giữa trục X và các nút, trong đó α

và
γ

nằm trong khoảng từ 0 đến
2π

và

β

nằm trong khoảng từ 0 đến
π
Hình 2.5 và

Hình 2.6 xét hệ tọa độ với các vector đơn vị (X, Y, Z).

Hình 2.4: Góc Euler

CHƯƠNG 2. CƠ SỞ LÝ THUYẾT

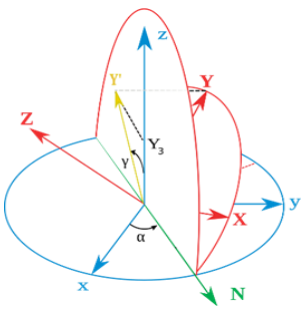
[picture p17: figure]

BỘ MÔN ĐIỀU KHIỂN TỰ ĐỘNG | 16

Hình 2.5: Hình chiếu của trục Z trên trục tiêu chuẩn

Với:

2
3 | 3 | 2 cos( ) Z , sin( ) | 1 Z , cos( ) sin( ) | Z β = | β = | − | α × | β = −

Từ các phương trình trên

α β γ ,,
được tính như dưới đây:

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
arccos( | )
1Z
arccos(Z )
Y
arccos( | )
1Z

−
α=
−
β=

γ=
−

(1.18)

Hình 2.6: Hình chiếu của trục Y trên trục tiêu chuẩn

2.2.5.2 Phương pháp Quaternion
Phương pháp Quaternion là một hệ thống số mở rộng các số phức. Phương trình

được mô tả lần đầu tiên bởi nhà toán học người Ireland William Rowan Hamilton vào

năm 1843 và áp dụng cho cơ học trong không gian ba chiều. Quaternion được ký hiệu

là q được định nghĩa theo phương trình sau:

CHƯƠNG 2. CƠ SỞ LÝ THUYẾT

BỘ MÔN ĐIỀU KHIỂN TỰ ĐỘNG | 17 [ | ]

T
0 | 1 | 2 | 3
2 | 2 | 2 | 2 | 2
| 0 | 1 | 2 | 3
q | q | q | q | q
q | q | q | q | q | 1

=

= | + | + | + | =

(1.19)

Áp dụng cho phép quay trong không gian, với vector trục u (

2 | 2 | 2 | 1
x | y | z
u | u | y + | + | =
, u là

vector đơn vị) và góc quay
θ

ta sẽ có một phép xoay quaternion. Sau đó, chúng tôi tính được một ma trận xoay trong không gian ba chiều.

2 | 2
2 | 3 | 1 2 | 0 3 | 0 2 | 1 3
| | | 2 | 2
xyz | 1 2 | 0 3 | 1 | 3 | 2 3 | 0 1
2 | 2
1 3 | 0 2 | 0 1 | 1 2 | 1 | 2
| 1 2 (q | q ) 2 (q q | q q ) 2 (q q | q q )
R | 2 (q q | q q ) 1 2 (q | q ) 2 (q q | q q )
| 2 (q q | q q ) 2 (q q | q q ) 1 2 (q | q )
é | ù − × | + | × | − | × | − ê | ú
= | × | − | − × | + | × | − ê | ú
ê | ú × | − | × | − | − × | + ë | û

(1.20)

Sử dụng phương pháp Quaternion sẽ giúp giải quyết vấn đề khóa chống rung. Bộ

phận khóa chống rung là sự mất đi một bậc tự do trong cơ chế ba chiều, ba góc, xảy ra

khi trục của hai trong số ba gimbal được dẫn động thành một cấu hình song song, "khóa"

hệ thống quay trong một không gian chu kỳ suy biến. Giá trị sau khi được đo bằng cảm

biến sau đó có thể được xử lý bằng bộ vi xử lý. Các giá trị có thể nhận được có giá trị

quaternion. Tuy nhiên, dựa trên quaternion, chúng ta không thể hình dung được các góc

của độ nghiêng.
Vì vậy, chúng ta cần chuyển đổi từ góc quaternion sang góc Euler (yaw, pitch, roll)

với công thức như sau:

0 1 | 2 3
2 | 2
1 | 2
0 2 | 1 3
0 3 | 1 2
2 | 2
2 | 3
2 (q q | q q )
arctan
1 2 (q | q )
arcsin(2 (q q | q q )
2 (q q | q q )
arctan
1 2 (q | q )
é | ù × | +
ê | ú éù φ | − × | + ê | ú êú θ = | × | − ê | ú êú ê | ú êú ëû ψ | × | + ê | ú
ê | ú − × | + ë | û

(1.21)

### 2.3 BỘ ĐIỀU KHIỂN PID

### 2.3.1 Định nghĩa

Bộ điều khiển PID (Proportional Integral Derivative) là một cơ chế phản hồi vòng

điều khiển rộng rãi trong các hệ thống điều khiển vòng kín.

Bộ điều khiển sẽ tính toán giá trị sai số giữa giá trị đo thông số biến đổi và giá trị

đặt mong muốn. Bộ điều khiển sẽ thực hiện giảm tối đa sai số bằng cách điều chỉnh giá

trị điều khiển đầu vào. Để đạt được kết quả tốt nhất, các thông số PID sử dụng trong

CHƯƠNG 2. CƠ SỞ LÝ THUYẾT

BỘ MÔN ĐIỀU KHIỂN TỰ ĐỘNG | 18

tính toán phải điều chỉnh theo tính chất của hệ thống trong khi kiểu điều khiển là giống

nhau, các thông số phải phụ thuộc vào đặc thù của hệ thống.

Hình 2.7: Bộ điều khiển PID

Phương trình thuật toán PID là:

p | i | d
0
de(t) u(t) K | e(t) K e( )d | K
dt

τ
= | × | + | τ τ + ò
(1.22)

Trong đó:

K
p

là tham số điều chỉnh tỉ lệ, giúp tạo ra tín hiệu điều chỉnh tỉ lệ với sai lệch đầu

vào theo thời gian lấy mẫu.

Ki

là tham số tích phân của sai lệch theo thời gian lấy mẫu, điều khiển tích phân

là phương pháp điều chỉnh để tạo ra các tín hiệu điều chỉnh sao cho độ sai lệch giảm về

0.

Kd

là tham số vi phân của sai lệch. Điều khiển vi phân tạo ra tín hiệu điều chỉnh

sao cho tỉ lệ với tốc độ thay đổi sai lệch đầu vào.

e t | SP PV t ( ) | ( ) = | −

là sai số (SP là điểm đặt, PV là biến quá trình).

t là thời gian hoặc thời gian tức thời (hiện tại).
τ là biến tích hợp (nhận giá trị từ thời gian 0 đến t).

### 2.3.2 Chỉnh bộ điều khiển PID

Điều chỉnh một vòng điều khiển là việc điều chỉnh các thông số điều khiển của nó

(tỷ lệ độ lợi, độ lợi tích phân, độ lợi đạo hàm) đến các giá trị tối ưu cho điều khiển mong

muốn phản ứng. Tính ổn định là một yêu cầu cơ bản. Nhưng ngoài ra, các hệ thống khác

nhau có các nhu cầu khác nhau, các ứng dụng khác nhau có các yêu cầu khác nhau và

các yêu cầu có thể xung đột với nhau. Điều chỉnh PID là một vấn đề khó khăn, thậm chí

CHƯƠNG 2. CƠ SỞ LÝ THUYẾT

BỘ MÔN ĐIỀU KHIỂN TỰ ĐỘNG | 19

mặc dù chỉ có ba tham số, vì nó phải đáp ứng các tiêu chí phức tạp trong những hạn chế

của điều khiển PID.

Có một số phương pháp để điều chỉnh vòng lặp PID. Các phương pháp hiệu quả

nhất thường liên quan đến việc phát triển một số dạng mô hình quy trình, sau đó chọn

P, I và D dựa trên các tham số của mô hình động. Các phương pháp điều chỉnh thủ công

có thể được tương đối tốn thời gian, đặc biệt là đối với các hệ thống có thời gian lặp dài.

Sự lựa chọn của phương thức sẽ phụ thuộc phần lớn vào việc vòng lặp có thể được thực

hiện "ngoại tuyến" cho điều chỉnh và về thời gian phản hồi của hệ thống. Nếu hệ thống

có thể được đưa vào ngoại tuyến, phương pháp điều chỉnh tốt nhất thường liên quan đến

việc yêu cầu hệ thống thực hiện một bước thay đổi trong đầu vào, đo lường đầu ra như

một hàm của thời gian và sử dụng phản hồi này để xác định thông số điều khiển.

### 2.4 BỘ LỌC KALMAN

### 2.4.1 Giới thiệu về bộ lọc Kalman

Hầu hết các hệ thống hiện đại được trang bị nhiều cảm biến cung cấp ước tính các

biến ẩn (chưa biết) dựa trên một loạt các phép đo. Ví dụ: máy thu GPS cung cấp ước

tính vị trí và vận tốc, trong đó vị trí và vận tốc là các biến ẩn và chênh lệch thời gian của

tín hiệu đến của các vệ tinh là phép đo.

Một trong những thách thức lớn nhất của hệ thống theo dõi và kiểm soát là cung

cấp đúng và chính xác các dự đoán của biến ẩn khi không chắc chắn dữ liệu. Trong máy

thu GPS, độ không đảm bảo của máy phụ thuộc vào nhiều yếu tố bên ngoài như nhiễu

nhiệt, hiệu ứng khí quyển, sự thay đổi nhỏ của vị trí vệ tinh, độ chính xác của đồng hồ

máy thu và nhiều yếu tố khác.

Kalman Filter là một trong những thuật toán ước lượng quan trọng và phổ biến

nhất. Bộ lọc Kalman tạo ra các ước tính về các biến ẩn dựa trên các phép đo không chính

xác và không chắc chắn. Ngoài ra, Kalman Filter còn cung cấp dự đoán về tương lai của

trạng thái của hệ thống dựa trên các dự báo trong quá khứ.

### 2.4.2 Bộ lọc Kalman một chiều

Bộ lọc Kalman Filter một chiều tức là bộ lọc chỉ có thể theo dõi một biến trạng

thái, chẳng hạn như khoảng cách hay vị trí trên trục tọa độ. Với mục đích ổn định tín

hiệu theo một chiều nào đó, bộ lọc Kalman Filter được sử dụng. Một bộ lọc Kalman

CHƯƠNG 2. CƠ SỞ LÝ THUYẾT

BỘ MÔN ĐIỀU KHIỂN TỰ ĐỘNG | 20

gồm có hai quá trình bao gồm ước đoán trạng thái và điều chỉnh dự đoán dựa vào kết

quả đo.
Với bộ lọc Alpha dùng để ước lượng vị trí và Beta dùng để tính toán tốc độ thay

đổi của dữ liệu. Bộ lọc

αβ − là một dạng bộ lọc được đơn giản hóa để ước tính và làm

mịn dữ liệu điều khiển. Nó liên quan chặt chẽ đến bộ lọc Kalman và các bộ quan sát

trạng thái tuyến tính được sử dụng trong lý thuyết điều khiển. Ưu điểm chính của nó là

không yêu cầu một mô hình hệ thống chi tiết. Bộ lọc

αβ − giả định rằng một hệ thống

được xấp xỉ đầy đủ bởi một mô hình có hai trạng thái bên trong, trong đó trạng thái đầu

tiên thu được bằng cách tích hợp giá trị của trạng thái thứ hai theo thời gian.

Hình 2.8: Sơ đồ khối một quá trình lọc của bộ lọc Kalman

### 2.4.3 Phương pháp lập trình đa luồng

Thread là một đơn vị cơ bản trong CPU. Một luồng sẽ chia sẻ với các luồng khác

trong cùng process về thông tin data, các dữ liệu của mình. Việc tạo ra thread giúp cho

các chương trình có thể chạy được nhiều công việc cùng một lúc. Hay nói một cách đơn

giản, Thread là các hàm hay thủ tục chạy độc lập đối với chương trình chính. Một process

dĩ nhiên có thể chứa nhiều thread bên trong nó. Điểm quan trọng nhất cần chú ý là một

thread có thể làm bất cứ nhiệm vụ gì một process có thể làm.

CHƯƠNG 2. CƠ SỞ LÝ THUYẾT

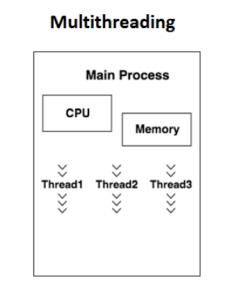
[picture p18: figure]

BỘ MÔN ĐIỀU KHIỂN TỰ ĐỘNG | 21

Hình 2.9: Phương pháp xử lý đa luồng

### 2.5 PHƯƠNG PHÁP OPTICAL FLOW

### 2.5.1 Lý thuyết

Optical flow có thể ánh xạ chuyển động ba chiều cường độ sáng của các điểm

thành mặt phẳng hình ảnh hai chiều. Optical Flow được tính toán bằng cách giả sử độ

sáng của một điểm hình ảnh cụ thể là không đổi theo thời gian (độ sáng không đổi).

Một điểm trong hình ảnh (x, y) di chuyển đến tọa độ mới (x + dx, y + dx) trong

khoảng thời gian dt, trong đó (dx, dy) là sự thay đổi của điểm này theo hai hướng không

gian (x và y tương ứng). Độ sáng tại điểm (x, y) tại thời điểm t được ký hiệu là
I x y t ( , , )

.Do đó, phương trình hằng số độ sáng sẽ là:

I x y t | I x dx y dy t dt ( , , ) | ( | , | , | ) = | + | + | +
(1.23)

Giả sử độ thay đổi pixel dx và dy là nhỏ, xấp xỉ (1.23) bằng chuỗi Taylor bậc một

( | , | , | ) | ( , , ) | I | I | I I x dx y dy t dt | I x y t | dx | dy | dt
x | y | t
∂ | ∂ | ∂
+ | + | + | = | + | + | + ∂ | ∂ | ∂

(1.24)

Chia (1.24) cho

dt
, ta thu được:
I u I v I x | y | t + | + = 0
(1.25)

Trong đó,
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
là đạo hàm riêng của x,y và t.

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
là tốc độ của optical flow.

CHƯƠNG 2. CƠ SỞ LÝ THUYẾT

BỘ MÔN ĐIỀU KHIỂN TỰ ĐỘNG | 22

### 2.5.2 Thuật toán Lucas-Kanade

Dựa vào Lucas-Kanade, giả thiết rằng sự thay đổi của các pixel trong một vùng

lân cận nhỏ là như nhau.
Phương trình (1.25) là một phương trình gồm 2 ẩn số. Do đó, để giải phương trình

(1.25), các pixel lân cận sẽ được xem xét tính toán và áp dụng phương pháp bình phương tối thiểu được áp dụng để giải hệ phương trình này. Phương trình cho các pixel trong

vùng lân cận được xem xét có thể được trình bày dưới dạng ma trận (1.26). Nếu ma trận

khả nghịch,

( , ) uv

có thể thu được:

1
II | II | II u | xx | xy | x t
v | II | II | II xy | yy | y t
é | ù é | ù éù | ê | ú ê | ú êú ëû | ê | ú ê | ú ë | û ë | û

−
∑ | ∑ | ∑
=−
∑ | ∑ | ∑

(1.26)

Tuy nhiên, đối với các đối tượng chuyển động nhanh, công thức (1.26) được trình

bày ở trên của thuật toán Lucas-Kanade là không đủ, vì trong trường hợp này, độ dịch chuyển pixel quá lớn và điều kiện phân tích vùng lân cận nhỏ bị sai. Trong tình huống

như vậy, một cách tiếp cận khác được sử dụng. Một kim tự tháp của hình ảnh được ra

tao cho mỗi khung hình trọng chuỗi video. Khung hình gốc được giảm đi hai lần, sau đó

hình ảnh mới được tạo lại giảm tiếp 2 lần.

Trong bước tiếp theo, optical flow được tính cho hình ảnh theo tỷ lệ nhỏ nhất theo

thuật toán Lucas-Kanade. Optical flow thu được được sử dụng để sửa đổi hình ảnh trước

đó theo tỷ lệ thelager. Đối với khung sau khi chuyển đổi và khung hiện tại, optical flow

được tính lại.
Toàn bộ quy trình được lặp lại cho đến khi optical flow được tính cho hình ảnh

đầu vào. Hình 2.10 trình bày sơ đồ theo sau các phép tính được thực hiện trên các thang

đo liên tiếp.

Hình 2.10: Pyramid Lucas-Kanade (PLK)

CHƯƠNG 2. CƠ SỞ LÝ THUYẾT

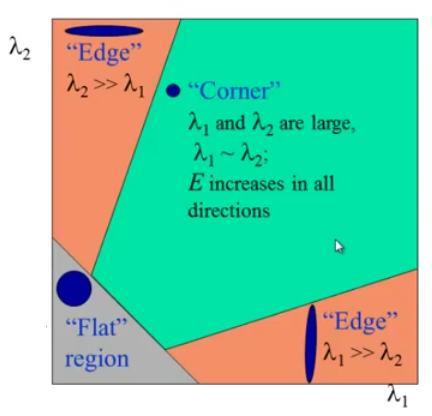
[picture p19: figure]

BỘ MÔN ĐIỀU KHIỂN TỰ ĐỘNG | 23

### 2.5.3 Theo dõi đặc trưng (feature tracking)

Đầu tiên, phương pháp phát hiện góc Shi-Tomasi được sử dụng để trích xuất cách

đặc trưng (keypoints) tốt phía bên dưới mặt đất. Phương pháp Shi-Tomasi phát triển dựa

trên phương pháp phát hiện góc Harris. Phương pháp pháp hiện góc của Harris và Shi-

Tomasi được trình bày (1.27) và (1.28):
1 2 | 1 | 2 R | k = | − | + λ λ | λ λ ( | )
(1.27)

R =min( , ) λλ1 2
(1.28)

Phương pháp xác định góc Harris và Shi-Tomasi biểu diễn trong không gian

λλ 1 | 2 − | được trình bày ở Hình 2.11 và Hình 2.12. Trong đó, vùng màu xám là mặt phẳng,

vùng màu cam là cạnh và vùng màu xanh là góc.

Hình 2.11: Phương pháp Harris corner

Hình 2.12: Phương pháp Shi-Tomashi corner

Từ đó, các đặc trưng này được đưa vào thuật toán Lucas-Kanade để tính toán sự

thay đổi của các đặc trưng (keypoints) này trong khung hình. Hệ thống sẽ nhận dạng lại

CHƯƠNG 2. CƠ SỞ LÝ THUYẾT

BỘ MÔN ĐIỀU KHIỂN TỰ ĐỘNG | 24

các đặc trưng mới bằng GFTT (sử dụng phương pháp Shi-Tomasi) khi số lượng đặc

trưng giảm xuống dưới ngưỡng cho phép. Ngưỡng số lượng đặc trưng được chọn là 10.

Tiếp theo, thuật toán PLK (Pyramid Lucas – Kanade) được chọn có 3 mức độ và

kích thước cửa sổ là
25 25 ×

pixel. Độ thay đổi của pixel trong khung sẽ được tính toán.

Lưu đồ thực hiện được hiển thị ở Hình 2.13.

Hình 2.13: Lưu đồ theo dõi đặc trưng

### 2.5.4 Cảm biến khoảng cách Lidar 1D

LIDAR là một trong những thiết bị gắn với các thiết bị tự hành, thiết bị này đóng

vai trò quan trọng trong hệ thống vì ứng dụng nhận thức thiết yếu. Vì tên đầy đủ là “Dò

tìm ánh sáng và phạm vi”, nguyên tắc làm việc rất dễ hiểu. Ngắn gọn, nó có liên quan

đến phương pháp tính toán cho phép xác định chướng ngại vật cách xa bao nhiêu so với

cảm biến. Hơn nữa, thiết bị thực sự sử dụng chùm tia laser để phân tích phát hiện và

mục đích theo dõi.

CHƯƠNG 2. CƠ SỞ LÝ THUYẾT

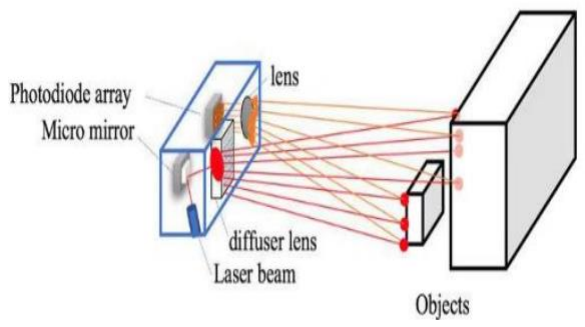
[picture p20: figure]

BỘ MÔN ĐIỀU KHIỂN TỰ ĐỘNG | 25

Hình 2.14: Nguyên lý hoạt động của Lidar 1D

Cụ thể, công nghệ LIDAR là công nghệ viễn thám dùng để đo khoảng cách giữa

mục tiêu và chính nó. Ánh sáng được phát ra từ thiết bị và đi đến mục tiêu. Nó sẽ phản

xạ khỏi bề mặt của nó và quay trở lại nguồn phát của nó. Nhờ có hằng số ánh sáng tốc

độ, khoảng cách sẽ được xác định bởi phương trình sau:

2

Vantocanhsang Thoigiandichuyen Khoangcach | ×
=

(1.29)

Ở nhiều khu vực có bề mặt đất phức tạp cản trở độ chính xác của cảm biến này.

Nhiều bản cập nhật mới trong máy sử dụng toán học trung bình để giải quyết vấn đề.

### 2.5.5 Mô hình pin-hole

Thế giới thực thường được chụp bằng ống kính máy ảnh, đó là lý do tại sao một

số mô hình để truyền thông tin giữa cả hai hệ thống được yêu cầu. Thông qua mô hình

pin-hole, chúng ta có thể liên kết tọa độ của máy ảnh (2D) với thế giới thực (3D) với sự

trợ giúp của các tham số vật lý như độ dài khoảng cách tiêu cự, kích thước pixel, tâm

hình ảnh và hướng camera. Các tham số nội tại liên quan đến hệ tọa độ lý tưởng của pin-

hole với tọa độ camera, các tham số này xác định hình học và quang học.

Để chiếu một điểm 3D vào mặt phẳng hình ảnh, các phương trình sau được sử

dụng:

0

0

0
w | 0 | 0 | 1
u | s u | x
v | v | y
z

α
β
é ù é | | ù é ù
ê ú ê | | ú ê ú
=
ê ú ê | | ú ê ú
ê ú ê | ú ê ú ë û ë | û ë û

(1.30)

Trong đó:

αβ,

là độ dài tiêu cự tính bằng pixel; 0 0 uv,

xác định trung tâm hình

ảnh bằng pixel; s là tham số nghiêng.

Chuẩn hóa phương trình biểu diễn pixel trên hình ảnh 2D:

CHƯƠNG 2. CƠ SỞ LÝ THUYẾT

BỘ MÔN ĐIỀU KHIỂN TỰ ĐỘNG | 26 1 | 1
2 | w
w | | | | 1
u | | | | p x
P | x | v | p y
é ù é | ù ′
ê ú ê | ú ′ = | = | = | ′
ê ú ê | ú
ê ú ê | ú ë û ë | û

(1.31)

Hình 2.15: Mô hình chiếu pin-hole

Các tham số bên ngoài liên quan đến hệ tọa độ của thế giới thực với tọa độ camera

của máy ảnh để xác định được hướng trong không gian. Nói chung, ma trận chiếu có thể

được phân tách thành các tham số bên ngoài và bên trong như sau:

x K R t X = [ | ]
(1.32)
0 | 11 | 12 | 13 | 1
0 | 21 | 22 | 23 | 2
| 31 | 31 | 33 | 3

0
w | 0 | 0 | 1
1

X
u | s u | r | r | r | t
Y
v | v | r | r | r | t
Z
| | r | r | r | t

α
β
éù é ù é | ùé | ùêú ê ú ê | úê | ú
= | êú ê ú ê | úê | úêú ê ú ê | úê | ú ë û ë | ûë | ûêú ëû
(1.33)

Trong đó, x là tọa độ của ảnh; K là ma trận nội tại; R là ma trận quay; t là ma trận chuyển đổi.

Khi mô hình được sử dụng, ánh xạ từ 3D sang 2D được gọi là "phép chiếu phối

cảnh". Hình 2.16 có 3 hệ quy chiếu được xem xét đến là hệ quy chiếu camera, hệ quy

chiếu hình ảnh và hệ quy chiếu của thế giới thực. Trong Hình 2.16, OC là gốc của hệ tọa

độ trong hệ quy chiếu của camera và Oi gọi là mặt phẳng hình ảnh, trong khi đó f được

gọi là độ dài tiêu cự biểu thị khoảng cách giữa tâm chiếu và hình ảnh.

CHƯƠNG 2. CƠ SỞ LÝ THUYẾT

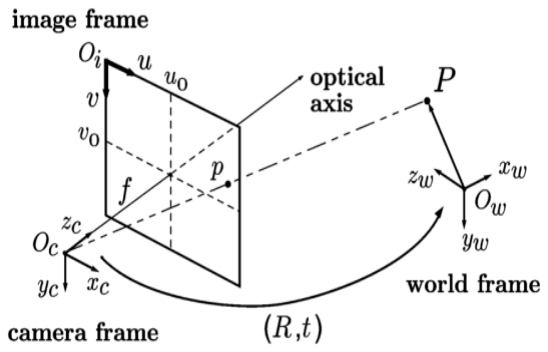
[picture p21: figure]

BỘ MÔN ĐIỀU KHIỂN TỰ ĐỘNG | 27

Hình 2.16: Hình chiếu phối cảnh của mô hình pin-hole

Một điểm trong không gian có tọa độ

( ,, )

T
P X Y Z =

đến mặt phẳng hình ảnh tương

ứng tọa độ p nối với một đường thẳng đạt đến tâm quang. Mối quan hệ vectơ giữa P và

p dễ dàng có được:

( , , | , )

T
T | fX fY X Y Z
Z | Z
æ | ö → ç | ÷ è | ø
(1.34)

Trong đó, vector

( pp x | y
, | )
đại diện cho tọa độ của điểm trên mặt phẳng hình ảnh.

Các tham số bên ngoài có thể thu được thông qua mối quan hệ giữa tọa độ của các

pixel và tọa độ tương đương của chúng trong thế giới thực, quá trình này được gọi là

hiệu chuẩn. Có nhiều kỹ thuật và phần mềm hiệu chuẩn có sẵn giúp cho quá trình này

trở nên rất đơn giản.

Thông qua mô hình pin-hole, độ dài tiêu cự f được tính toán. Thông số độ dài tiêu

cự rất quan trọng để chuyển đổi kích thước khung hình sang kích thước thực tế.

Giả sử quadcopter bay lơ lửng ở độ cao h, camera có góc là
α

và d là khoảng cách
camera có thể nhìn thấy được ở mặt đất (Hình 2.17). Khoảng cách camera nhìn thấy có

thể tính được nếu biết giá trị độ cao và độ dài tiêu cự.

CHƯƠNG 2. CƠ SỞ LÝ THUYẾT

BỘ MÔN ĐIỀU KHIỂN TỰ ĐỘNG | 28

Hình 2.17: Góc camera từ quadcopter chiếu xuống đất

Công thức chuyển đổi từ kích thước của khung hình sang kích thước trong thực tế

như sau:

x

x | w
| y
y | h
h | d
f | I
h | d
f | I

=

=

(1.35)

Trong đó,
w

I

là chiều dài của khung hình và dx

là chiều dài camera quan sát được

trong thực tế. Tương tự,
h

I

là chiều cao của khung hình và dy

là chiều cao camera quan

sát được trong thực tế.

CHƯƠNG 3. THIẾT KẾ HỆ THỐNG

BỘ MÔN ĐIỀU KHIỂN TỰ ĐỘNG | 29

## Chương 3. THIẾT KẾ HỆ THỐNG

### 3.1 YÊU CẦU PHẦN CỨNG

Mô hình được làm từ vật liệu nhẹ và bền để giảm trọng lượng của mô hình và tránh

tác động của sự cố. Tổng trọng lượng của mô hình là 1kg.

### 3.2 SƠ ĐỒ KHỐI HỆ THỐNG

Hình 3.1: Sơ đồ khối hệ thống

### 3.3 GIỚI THIỆU PHẦN CỨNG

Bảng 2: Danh sách thiết bị sử dụng trong đề tài

STT | Tên thiết bị | Số lượng | Thành tiền
1 | Khung máy bay QAV 250 | 1 | 290.000
2 | Động cơ không chổi than MT2204 - 2300KV | 4 | 360.000
3 | ESC 2S-4S 30A Dshot600 BLHeli-S | 4 | 800.000
4 | Mạch bay Mateksys F722-SE | 1 | 2.000.000

CHƯƠNG 3. THIẾT KẾ HỆ THỐNG

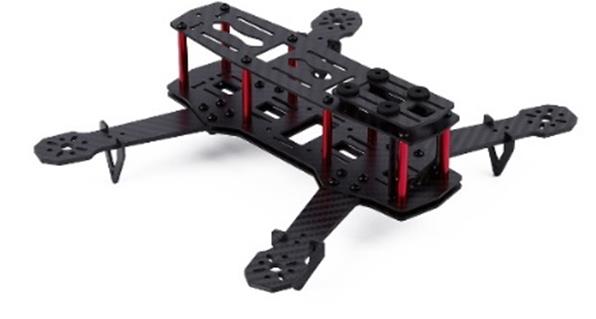
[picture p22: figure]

BỘ MÔN ĐIỀU KHIỂN TỰ ĐỘNG | 30
5 | Raspberry Pi 4 4GB | 1 | 3.560.000
6 | Cảm Biến Khoảng Cách TF-Luna ToF | 1 | 620.000
7 | Pin Lipo 3S | 1 | 400.000
8 | Mạch giảm áp Buck DC-DC | 1 | 40.000
9 | Camera Logitech C270 | 1 | 500.000
10 | Cánh quạt | 4 | 50.000
Tổng | | | 8.620.000

### 3.3.1 Khung máy bay QAV 250

Hình 3.2: Khung máy bay

Hình 3.3: Chi tiết cách lắp ráp khung QAV 250

Hình 3.2 và Hình 3.3 là hình của khung QAV250 và cách lắp ráp chi tiết của khung

máy bay. Trong mô hình này có khung máy bay trên được sử dụng và có thêm một số

chi tiết in 3d cho phù hợp với chức năng mô hình.

### 3.3.2 Động cơ không chổi than

3.3.2.1 Tổng quát

Mô hình sử dụng động cơ không chổi than. Động cơ không chổi than cung cấp một

số khả năng vượt trội so với động cơ có chổi than, bao gồm tỷ lệ mô-men xoắn trên

CHƯƠNG 3. THIẾT KẾ HỆ THỐNG

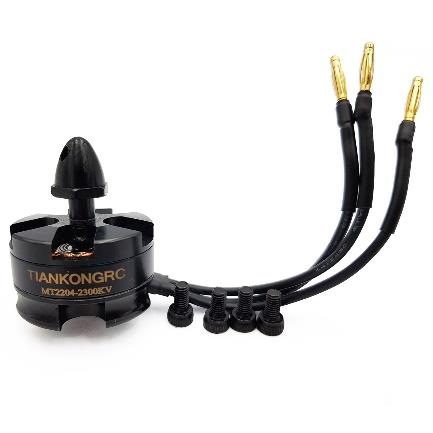
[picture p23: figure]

BỘ MÔN ĐIỀU KHIỂN TỰ ĐỘNG | 31

trọng lượng, nhiều mô-men xoắn hơn trên mỗi watt (tăng hiệu suất), tăng độ tin cậy,

giảm tiếng ồn, tuổi thọ cao hơn (không bị mòn chổi than và cổ góp), loại bỏ tia lửa ion

hóa từ cổ góp và giảm tổng thể nhiễu điện từ (EMI).

3.3.2.2 Động cơ không chổi than MT2204 - 2300KV

Hình 3.4: Động cơ không chổi than MT2204 - 2300KV

Bảng 3: Thông số kỹ thuật của động cơ không chổi than MT2204 - 2300KV

Thành phần | Thông số
Kích thước động cơ | 27.9 x 29.7 mm
RPM/V(KV) | 2300 KV
Công suất | 150W (30s)
Trục chính | M5*12mm
Khối lượng | 27g
Dòng chờ | 0.6A
Dòng cực đại | 12A

### 3.3.3 Mạch điều khiển tốc độ động cơ (Electronic speed controllers)

3.3.3.1 Tổng quát

Mạch điều khiển tốc độ động cơ (ESC) là một mạch điện tử điều khiển và điều

chỉnh tốc độ của động cơ điện. Nó cũng có thể đảo ngược chiều quay và phanh của động

cơ. ESC được sử dụng trong các mô hình điều khiển bằng tín hiệu điện. ESC tuân theo

tín hiệu tham chiếu tốc độ (xuất phát từ cần ga, cần điều khiển) và thay đổi tốc độ chuyển

CHƯƠNG 3. THIẾT KẾ HỆ THỐNG

BỘ MÔN ĐIỀU KHIỂN TỰ ĐỘNG | 32

mạch của các linh kiện transistors. Bằng cách điều chỉnh chu kỳ làm việc hoặc tần số

chuyển đổi của các transistors thì tốc độ của động cơ được thay đổi.

Để lựa chọn phù hợp một ESC, ta cần phải quan tâm vào các thông số về dòng

điện mà ESC có thể cung cấp. Nếu động cơ có công suất dòng điện lớn hơn dòng điện

định mức của ESC, sẽ có hiện tượng ESC bị nóng lên và gây hỏng vì dòng điện đi qua ESC quá với định mức. Ta nên chọn ESC có thể chịu đựng dòng điện đi qua lớn hơn

dòng điện của động cơ để đảm bảo ESC hoạt động tốt và không bị quá tải. Ngoài ra ta

cần phải quan tâm về protocol mà ESC sẽ sử dụng để giao tiếp với Flight contronller.

Có 2 dạng protocol chính để giao tiếp với ESC:

+ Analog protocols: Oneshot125, Oneshot42, Multishot

+ Digital protocol: DSHOT150, DSHOT300, DSHOT600

Hình 3.5: So sánh tốc độ các giao thức ESC

3.3.3.2 Mạch điều khiển tốc độ ESC 2S-4S 30A Dshot600 BLHeli-S

Hình 3.6: ESC 2S-4S 30A Dshot600 BLHeli-S

Bảng 4: Thông số kỹ thuật của ESC 2S-4S 30A Dshot600 BLHeli-S

CHƯƠNG 3. THIẾT KẾ HỆ THỐNG

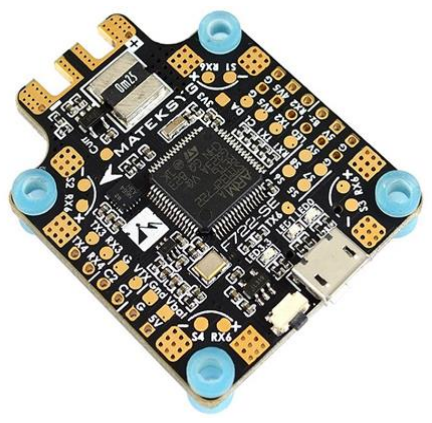
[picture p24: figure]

BỘ MÔN ĐIỀU KHIỂN TỰ ĐỘNG | 33
Thành phần | Thông số
Điện áp hỗ trợ | pin lithium 2-4S hoặc pin NiCd / NIMh 5-12 cell
Dòng làm việc | 30A đỉnh 40A
Thỏa thuận hỗ trợ | DSHOT125/300/600
Tốc độ làm mới | 600Hz
Kích thước | D24 * R12 mm
Khối lượng | 5.3g
Chương trình người dùng | BLHeli-S firmware

### 3.3.4 Bộ điều khiển bay Mateksys F722-SE

Bộ điều khiển bay là bộ phận quan trọng nhất của một mô hình bay, khi nó là bộ

phận quyết định các quá trình hành động của máy bay. Và mạch bay Mateksys F722-SE

là một mạch bay thương mại, có phần mềm mở để can thiệp và điều chỉnh các thông số.

Hình 3.7 là hình ảnh thực tế của mạch bay.

Hình 3.7: Mạch bay Mateksys F722-SE

Trên mạch tích hợp nhiều thành phần (vi xử lý trung tâm, cảm biến,…) và các IC

dùng để giao tiếp các chuẩn giao tiếp khác nhau. Vi xử lý trung tâm dùng để điều khiển

hoạt động bay. Các cảm biến tích hợp trên mạch có các cảm biến có chức năng như nhau

dùng để bổ trợ các tín hiệu trả về để hiệu chỉnh cảm biến chính xác hơn, có cảm biến áp

suất để tính toán độ cao. Chi tiết các phần tử thể hiện ở bảng 5.

CHƯƠNG 3. THIẾT KẾ HỆ THỐNG

BỘ MÔN ĐIỀU KHIỂN TỰ ĐỘNG | 34

Bảng 5: Chi tiết các thành phần trên mạch bay

Vi xử lý | STM32F722RET6
Cảm biến | IMU (gồm cảm biến góc quay Gyroscope và cảm biến gia tốc Accelerometer) | MPU6000 & ICM20602, Dual Gyros built-in (SPI)
| Cảm biến áp suất (Barometer) | BMP280
Khối lượng | | 10 g
Kích thước (dài x rộng x cao) | | 36x46mm

3.3.4.1 Vi xử lý trung tâm
STM32 là một trong những dòng chip phổ biến của hãng ST với nhiều dòng xử lý

khác nhau. Mạch STM32 có thể đọc đầu vào tín hiệu số hoặc tương tự trên cảm biến, có

các chuẩn giao tiếp như UART, I2C … Và từ các tín hiệu trên tính toán thành tín hiệu

đầu ra mục tiêu là kích hoạt động cơ, bật đèn led báo hiệu, gửi tín hiệu về máy tính.

Trong những năm qua, STM32 đã trở nên rất quen thuộc với sinh viên trong nhiều

môn học khác nhau, đến các kỹ sư thì dùng để phát triển các dự án. Bởi vì sự phát triển

nhanh chóng đó, liên quan đến cộng đồng STM đã phát triển đáng kể và thu hút rất nhiều

người tham gia.

Bảng 6: Thông số chi tiết của MCU

Vi xử lý | STM32F722RET6
Điện áp hoạt động | 1.7 – 3.6 V
Tần số hoạt động | 216 MHz
RAM | 256 kB
Số cổng I/O | 140 cổng
SRAM | 4 kB
Bộ nhớ Flash | 512 Kbytes
Số kênh ADC | 24 kênh
Số lượng của Timer/Counter | 18 kênh
Chuẩn giao tiếp | CAN, I2C, SAI, SPI, UART/USART, USB

CHƯƠNG 3. THIẾT KẾ HỆ THỐNG

BỘ MÔN ĐIỀU KHIỂN TỰ ĐỘNG | 35

3.3.4.2 Cảm biến trên mạch bay Mateksys F722-SE

Hình 3.8: Các cảm biến trên mạch bay

Hình 3.8 thể hiện vị trí các cảm biến có trên mạch Mateksys F722-SE bao gồm 3

cảm biến được tích hợp trên mạch, các cảm biến có trên mạch sử dụng tiêu chuẩn giao

tiếp I2C để đọc dữ liệu.

Bảng 7: Thông số kỹ thuật của cảm biến ICM20602

Vi điều khiển | ICM20602
ADC | 16 bits
Điện áp hoạt động | 1.71V – 3.45 V
Độ phân giải của gyro | ±250dps, ±500dps, ±1000dps, ±2000dps
Sai số độ nhạy của gyro | ±1%
Độ phân giải của accel | ±2g, ±4g, ±8g, ±16g
Giao tiếp | I2C, SPIs

Bảng 8: Thông số kỹ thuật của cảm biến MPU6000

Vi điều khiển | MPU 6000
Điện áp hoạt động | 2.4 – 3.6 V
Độ phân giải của gyro | ±250dps, ±500dps, ±1000dps, ±2000dps
Độ nhạy của gyro | 131, 65.5, 32.8, 16.4

CHƯƠNG 3. THIẾT KẾ HỆ THỐNG

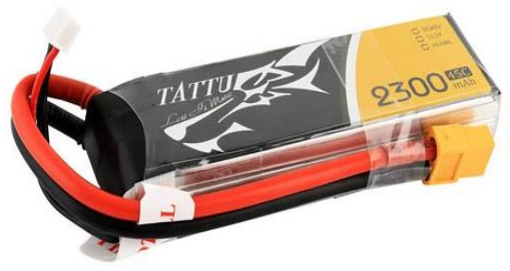
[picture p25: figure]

BỘ MÔN ĐIỀU KHIỂN TỰ ĐỘNG | 36
Độ phân giải của accel | ±2g, ±4g, ±8g, ±16g
Độ nhạy của accel | 16384, 8192, 4096, 2048
Giao tiếp | I2C

Bảng 9: Thông số kỹ thuật của cảm biến BMP280

Vi điều khiển | BMP280
Điện áp hoạt động | 3.3V
Dòng tiêu thụ | 0,6 mA
Khoảng đo nhiệt độ | -40 - +85°C
Khoảng đo áp suất | 300 - 1100 hPa
Hệ số bù nhiệt độ | 12.6 cm/K
Giao tiếp | I2C

### 3.3.5 Pin Lipo 3S

Pin Lithium Polymer (được gọi là pin “LiPo”), là một loại pin mới hiện được sử dụng trong nhiều thiết bị điện tử tiêu dùng. Chúng đã trở nên phổ biến trong ngành điều

khiển vô tuyến trong vài năm qua và hiện là sự lựa chọn phổ biến nhất cho bất kỳ ai

đang tìm kiếm thời gian hoạt động lâu dài và công suất cao của mô hình.

Chúng là loại pin có thể sạc đầy lại của công nghệ lithium-ion sử dụng chất điện

phân polymer thay vì chất điện phân lỏng. Các polymer mềm (gel) có độ dẫn điện cao

tạo thành chất điện ly này. Loại pin này cung cấp năng lượng định mức cao hơn so với

các loại pin lithium khác. Hình 2.9 là loại pin Lipo 3S 2300mAh.

Hình 3.9: Pin Lipo 3S 2300mAh

CHƯƠNG 3. THIẾT KẾ HỆ THỐNG

BỘ MÔN ĐIỀU KHIỂN TỰ ĐỘNG | 37

Bảng 10: Thông số kỹ thuật của Pin Lipo 3S 2300mAh

Thành phần | Thông số
Số volt | 11.1V
Dung lượng | 2300mAh
Tỷ lệ xả | 45C
Trọng lượng tịnh (g) | 182,2 ± 20g
Tốc độ xả tối đa | 90C
Kích thước | 106x34x23mm
Loại kết nối | XT60
Chiều dài dây | 100mm
Dòng tối đa (A) | 103.5
Dòng Max Burst (A) | 207

### 3.3.6 Cánh quạt

3.3.6.1 Tổng quan

Mục đích của cánh quạt quadcopter là tạo ra lực đẩy và mô-men xoắn để giữ cho

quadcopter bay và di chuyển. Thông thường, các cánh quạt quadcopter tạo ra nhiều lực

đẩy hơn khi chúng quay nhanh hơn. Chúng cũng bị ảnh hưởng bởi động lực bay của

chiếc quadcopter của bạn. Một số cánh quạt tạo ra nhiều lực đẩy hơn khi máy bay không

người lái đứng yên, trái ngược với khi nó đang bay. Các cánh quạt hoạt động tốt hơn

nhiều nếu tốc độ cao hơn. Quadcopter có hai loại cánh quạt và động cơ khác nhau. Một

bộ được thiết kế để quay theo chiều kim đồng hồ, trong khi bộ còn lại được thiết kế để

quay ngược chiều kim đồng hồ.

Chiều dài của khung quadcopter sẽ xác định kích thước tối đa của cánh quạt có thể

sử dụng. Điều này có thể dễ dàng được xác định bằng cách lấy chiều dài hoặc chiều rộng

nhỏ nhất của khung quadcopter chia cho hai. Và chiều dài cần nhỏ hơn một chút để tạo

khoảng trống quay giữa các cánh quạt liền kề.

Hai cánh quạt có hai cánh giúp tạo ra lực đẩy hiệu quả hơn. Bên cạnh đó, có cánh

quạt ba cánh, bốn cánh hoặc nhiều cánh hơn. Đối với mục đích của cánh quạt

quadcopter, số lượng cánh quạt không phải là một vấn đề lớn.

CHƯƠNG 3. THIẾT KẾ HỆ THỐNG

BỘ MÔN ĐIỀU KHIỂN TỰ ĐỘNG | 38

Hình 3.10: Kích thước của cánh quạt

3.3.6.2 Cánh GEMFAN FLASH 5.1 Inch

Hình 3.11 là cánh quạt được sử dụng trong mô hình.

Hình 3.11: Cánh quạt ba lá GEMFAN 5.1 Inch

### 3.3.7 Camera Logitech C270

Hình 2.12 là hình ảnh camera sử dụng trong mô hình.

Hình 3.12: Camera Logitech C270

Bảng 11: Thông số kỹ thuật của Camera Logitech C270

CHƯƠNG 3. THIẾT KẾ HỆ THỐNG

BỘ MÔN ĐIỀU KHIỂN TỰ ĐỘNG | 39
Kiểu kết nối | USB
Chuẩn kết nối | USB 2.0
USB VID_PID | VID_046 & PID_081A
Thu âm | Tích hợp, chống ồn
Loại ống kính và cảm biến | Nhựa
Loại chỉnh hội tụ | Chỉnh được
Góc ống kính | 60
Độ dài tiêu cự | 4 mm
Độ phân giải | 1280 x 960 1.2MP
Số khung hình | 30 fps
Chiều dài cáp | 1.5 m

### 3.3.8 Raspberry Pi 4 Model B và mạch nguồn

3.3.8.1 Raspberry Pi 4 Model B
Raspberry Pi là một máy tính giá thành rẻ, có kích thước bằng thẻ tín dụng, có thể

cắm vào màn hình máy tính hoặc TV và sử dụng bàn phím và chuột một cách bình

thường. Nó là một thiết bị nhỏ có khả năng cho phép mọi người ở mọi lứa tuổi khám

phá máy tính và học cách lập trình bằng các ngôn ngữ như Scratch và Python. Nó có

khả năng làm mọi thứ như máy tính để bàn hoặc máy tính xách tay, từ duyệt Internet và

phát video độ phân giải cao, đến tạo bảng tính, xử lý văn bản và chơi trò chơi nhẹ.

Hơn nữa, Raspberry Pi có khả năng tương tác với thế giới bên ngoài và đã được

sử dụng trong một loạt các dự án trong thực tế, từ máy phát nhạc và máy phát hiện người

cho đến các trạm thời tiết. Raspberry Pi 4 Model B là mẫu đầu tiên của Raspberry Pi thế

hệ thứ thư. Nó đã thay thế Raspberry Pi 3 Model B vào tháng 11 năm 2020. Các tính

năng nổi bật:

+ Broadcom BCM2711, Quad core Cortex-A72 (ARM v8) 64-bit 1.5GHz.

+ 1GB RAM.
+ Wifi chuẩn 2.4 GHz và 5.0 GHz IEEE 802.11ac. Bluetooth 5.0, BLE.

+ 40 chân giao tiếp.

+ 2 cổng Micro HDMI 4K.

+ 2 cổng USB 3.0 và 2 cổng USB 2.0.

+ Nguồn vào USB-C 3A.

CHƯƠNG 3. THIẾT KẾ HỆ THỐNG

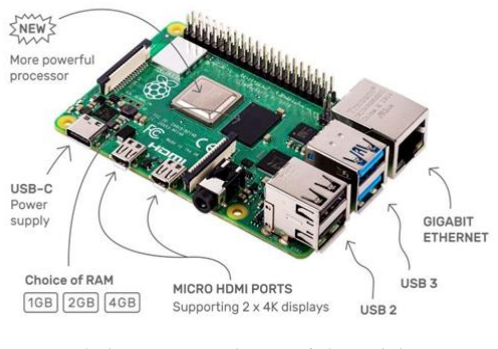
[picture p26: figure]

BỘ MÔN ĐIỀU KHIỂN TỰ ĐỘNG | 40

Hình 3.13: Raspberry Pi 4 model B

3.3.8.2 Raspberry Pi 4 Model B

Hình 3.14: Mạch hạ áp cho Raspberry

Bảng 12: Thông số kỹ thuật của mạch hạ áp

Đầu vào | 6 – 36 VDC
Đầu ra | 5 VDC
Đòng đầu ra | 3 A
Hiệu suất | 95 %
Ngõ ra dạng | 2 x USB
Kích thước (dài x rộng x cao) | 59x21x17mm

### 3.3.9 Cảm biến khoảng cách TF-Luna ToF

Cảm biến khoảng cách DFRobot TF-Luna ToF Micro Single-point Ranging

LiDAR có kích thước nhỏ gọn được sử dụng để đo khoảng cách bằng ánh sáng Laser

với độ chính xác cao từ 0.2m đến 8m, cảm biến sử dụng giao tiếp UART và I2C rất dễ

giao tiếp và lập trình, thích hợp với các ứng dụng xe tránh vật cản, robot thông minh,

lidar,…

CHƯƠNG 3. THIẾT KẾ HỆ THỐNG

BỘ MÔN ĐIỀU KHIỂN TỰ ĐỘNG | 41

Hình 3.15: Cảm biến khoảng cách TF-Luna ToF

Bảng 13: Thông số kỹ thuật của cảm biến khoảng cách TF-Luna ToF

Tín hiệu ra | Analog
Tần số | 100Hz
Khoảng cách đo | 0.2 ~ 8m
Độ phân giải | 1cm
Nguồn | 5V
Giao tiếp | UART/I2C

### 3.3.10 Mạch chuyển USB UART PL2303

Mạch chuyển USB UART PL2303 có tác dụng giao tiếp máy tính với thiết bị ngoài

thông qua chuẩn giao tiếp UART.

Hình 3.16: Mạch chuyển USB UART PL2303

Bảng 14: Thông số kỹ thuật của mạch chuyển USB UART PL2303

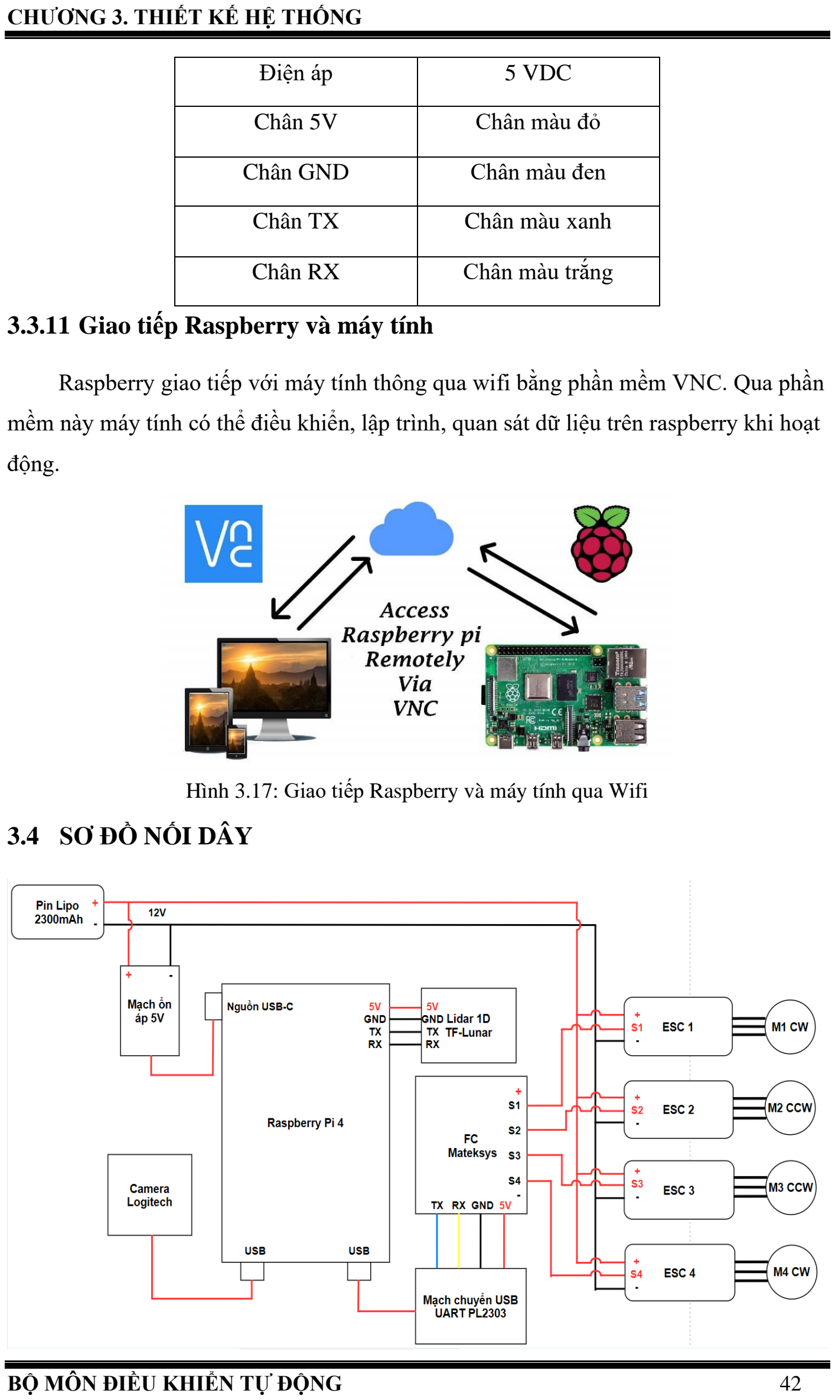
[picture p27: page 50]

CHƯƠNG 3. THIẾT KẾ HỆ THỐNG

BỘ MÔN ĐIỀU KHIỂN TỰ ĐỘNG | 42
Điện áp | 5 VDC
Chân 5V | Chân màu đỏ
Chân GND | Chân màu đen
Chân TX | Chân màu xanh
Chân RX | Chân màu trắng

### 3.3.11 Giao tiếp Raspberry và máy tính

Raspberry giao tiếp với máy tính thông qua wifi bằng phần mềm VNC. Qua phần

mềm này máy tính có thể điều khiển, lập trình, quan sát dữ liệu trên raspberry khi hoạt

động.

Hình 3.17: Giao tiếp Raspberry và máy tính qua Wifi

### 3.4 SƠ ĐỒ NỐI DÂY

CHƯƠNG 3. THIẾT KẾ HỆ THỐNG

BỘ MÔN ĐIỀU KHIỂN TỰ ĐỘNG | 43

Hình 3.18: Sơ đồ nối dây

### 3.5 XÂY DỰNG PHẦN CỨNG

Hình 3.19: Tổng quan phần cứng drone

CHƯƠNG 4. THUẬT TOÁN ĐIỀU KHIỂN

BỘ MÔN ĐIỀU KHIỂN TỰ ĐỘNG | 44

## Chương 4. THUẬT TOÁN ĐIỀU KHIỂN

### 4.1 THIẾT KẾ BỘ LỌC KALMAN

Ở trong đề tài này, bộ lọc Kalman được sử dụng để lọc tín hiệu đọc về từ cảm biến

khoảng cách TF Lunar 1D. Sau khi cất cánh được một thời gian rất ngắn, Quadcopter

cần phải định vị trong không gian. Chính vì vậy, cảm biến khoảng cách được sử dụng

để đo khoảng cách từ quadcopter đến mặt đất và gửi về máy tính trung tâm để xử lý. Do

chỉ có một giá trị đầu vào, nên sử dụng bộ điều khiển
αβ − đã trình bày ở Chương 2.

Các biến số được sử dụng để tính toán được nêu lên trong dưới đây:

Bảng 15: Bảng các thông số của bộ lọc

x | Giá trị độ cao thực tế (m)
z n | Giá trị độ cao được đo tại thời gian n (m)
x nn, | Giá trị độ cao ước lượng tại thời điểm n(m)
nn,1 x − | Giá trị độ cao ước lượng trước đó(m)
αβ − | Thông số cố định (m)
t | Thời gian lấy mẫu(s)

Tại thời điểm n, giá trị ước lượng:

, | ( 1 | 2 | 1 | ) | ( )

1

1 | 1

n

nn | n | n | i
i
x | z | z | z | z | z
n | n

Ù

−
=
= | + | + + | + | = ∑
(1.36)

Công thức ước lượng vị trí cho bộ lọc

| | α
:
, | , 1 | , 1 ( | )
n n | n n | n | n n
x | x | z | x = | + | − − | − α

(1.37)

Công thức ước lượng vận tốc cho bộ lọc β
:

,1
, 1 | , 1
n | n n
n n | n n
z | x
x | x
t

β

−
− | −
æ | ö −
= | + ç | ÷ è | ø Δ

(1.38)

Ta có được phương trình đạo hàm khoảng cách là vận tốc:

dx
xv
dt

==

(1.39)

CHƯƠNG 4. THUẬT TOÁN ĐIỀU KHIỂN

BỘ MÔN ĐIỀU KHIỂN TỰ ĐỘNG | 45

Phương trình ngoại suy trạng thái được mô tả như sau:

n | n | n 1
x | x | tx + = | + Δ

(1.40)

Mỗi khi LIDAR tính toán khoảng cách dựa trên tốc độ ánh sáng và thời gian bay,

kết quả nhận được sẽ được sử dụng để tính toán ước tính hiện tại sử dụng phương trình

cập nhật trạng thái cho cả chiều cao và tốc độ thay đổi chiều cao. Sau đó, phương trình

ngoại suy trạng thái sẽ được dùng để ước tính trạng thái tiếp theo.

Sự khác biệt giữa các giá trị ước tính và giá trị thực, do sai số ước tính thể hiện, sẽ

ngày càng nhỏ dần đến mức nhỏ nhất có thể. Tuy nhiên, sai số ước lượng không dễ tìm

nên độ không đảm bảo trong ước lượng là một cách tiếp cận khác, ký hiệu là r. Bằng

cách làm theo cách này, Kalman gain sẽ được tính theo:

( | )

,1

,1

, 0 | 1 nn
n | n
n n | n

p
K | K
p | r

−

−

= | ≤ | ≤
+

(1.41)

Phương trình cập nhật trạng thái và ngoại suy trạng thái được cập nhật dựa trên

Kalman gain:
( | )
( | )
, | , 1 | , 1
, 1 | , 1
n n | n n | n | n | n n
n | n n | n n
x | x | K z | x
| | K x | K
− | −

−

= | + | −
= − | | +

(1.42)

2
1 | 1, | , | ,
| | | x | | x | v
n | n | n | n | n | n n | n n
x | x | tx | p | p | t p + | + = | + Δ | Þ | = | + Δ

(1.43)

### 4.2 THUẬT TOÁN OPTICAL FLOW

Thuật toán xử lý ảnh được sử dụng trong đề tài được trình bày như lưu đồ dưới

đây:

CHƯƠNG 4. THUẬT TOÁN ĐIỀU KHIỂN

BỘ MÔN ĐIỀU KHIỂN TỰ ĐỘNG | 46

Hình 4.1: Lưu đồ thuật toán xử lý ảnh

Lưu đồ trên thể hiện toàn bộ quá trình của việc tìm vector dịch chuyển để tạo ra

giá trị đầu vào cho việc giữ cân bằng. Đầu tiên, camera sẽ đọc frame ảnh đầu tiên, sau

đó làm phẳng ảnh từ những thông số sau khi Calibration camera bởi vì ảnh lấy về từ

camera sẽ bị cong nên vector dịch chuyển sẽ không chính xác. Sau đó, chuyển frame

ảnh sang hệ ảnh xám. Vì sau khi làm phẳng ảnh, ở viền ảnh sẽ xuất hiện cũng góc cắt

khiến cho thuật toán Harris Corner sẽ nhận diện nó là một keypoint sẽ gây ra sai sót

trong quá trình tính toán vector. Chính vì vậy, chúng ta phải cắt lấy phần trung tâm. Sau

đó, dùng thuật toán Harris Corner tìm ra các keypoint trong các Frame ảnh. Sau đó, sử dụng thuật toán Optical flow để tính toán độ dịch chuyển giữa các frame và nhận được

giá trị Vector dịch chuyển tương ứng.

CHƯƠNG 4. THUẬT TOÁN ĐIỀU KHIỂN

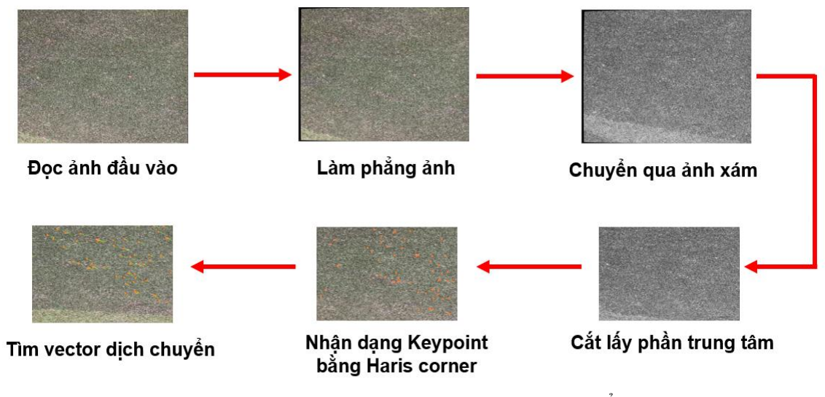
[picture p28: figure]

BỘ MÔN ĐIỀU KHIỂN TỰ ĐỘNG | 47

Hình 4.8: Quá trình tính toán Vector dịch chuyển

Tuy nhiên, vẫn có trường hợp làm cho quá trình bị kết thúc. Đó chính là khi

Quadcopter dịch chuyển cách điểm ban đầu quá xa (50cm) thì thuật toán xử lý ảnh sẽ

kết thúc. Khi đó, Quadcopter sẽ cập nhật lại các Keypoints và bắt đầu lại quá trình xử

lý ảnh.

### 4.3 XÂY DỰNG BỘ ĐIỀU KHIỂN PID

Bộ điều khiển đầu tiên là bộ điều khiển độ cao. Để Quadcopter giữ được độ cao,

thì giá trị tín hiệu cần điều khiển đó chính là giá trị xuất xung điều khiển Throttle. Để

Quadcopter có thể giữ được độ cao mong muốn, giá trị bộ điều khiển PID cần phải được

hiệu chỉnh sao cho giá trị Throttle được tính toán xung quanh điểm làm việc cân bằng.

Dưới đây là Hình 4.2 trình bày sơ đồ khối bộ điều khiển PID nhằm giữ độ cao cho

Quadcopter ở vị trí chiều cao mong muốn.

Hình 4.2: Sơ đồ bộ điều khiển độ cao

CHƯƠNG 4. THUẬT TOÁN ĐIỀU KHIỂN

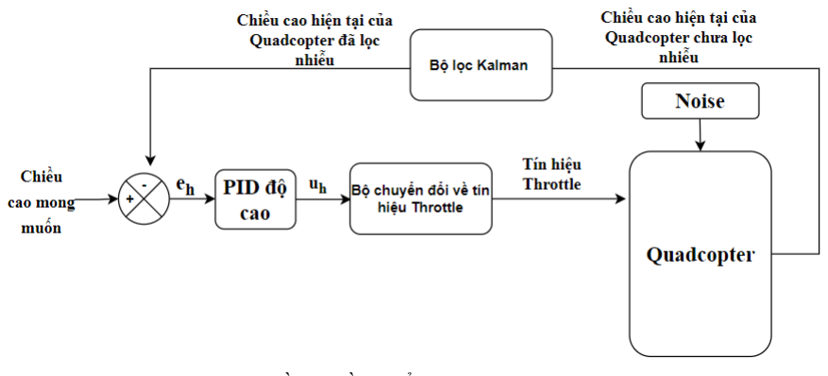
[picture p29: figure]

BỘ MÔN ĐIỀU KHIỂN TỰ ĐỘNG | 48

Tuy nhiên, các giá trị đọc về từ Lidar 1D đôi khi có nhiễu gây ra các sai số so với

thực tế. Điều này ảnh hưởng trực tiếp đến kết quả tính toán của bộ điều khiển độ cao

của Quadcopter. Chính vì vậy, bộ lọc Kalman Filter được thêm vào để lọc tín hiệu trả

về từ Lidar 1D là cần thiết trước khi đưa trở về bộ điều khiển để tính toán. Sơ đồ bộ điều

khiển PID có thêm bộ lọc Kalman được trình bày ở Hình 4.3.

Hình 4.3: Sơ đồ bộ điều khiển độ cao có thêm bộ lọc Kalman

Công thức điều khiển độ cao được trình bày như sau:

0

() ()

h d

t

h | ph h | ih | h | dh
e | h | h
de t PID | K e t | K | e dt K
dt
= | −
= | + | + ò

(1.44)

Trong đó:

+
h

e

sai số giữa giá trị đặt
d h

và giá trị đo được từ Lidar 1D h .

+
Kph

, Kih

, Kdh

lần lượt là hệ số tỉ lệ, hệ số tích phân và hệ số đạo hàm .

Lưu đồ trình bày quá trình vận hành bộ điều khiển độ cao được trình bày như

hình dưới:

CHƯƠNG 4. THUẬT TOÁN ĐIỀU KHIỂN

BỘ MÔN ĐIỀU KHIỂN TỰ ĐỘNG | 49

Hình 4.4: Lưu đồ bộ điều khiển PID giữ độ cao

Ở thời điểm bắt đầu, kiểm tra đã nhấn ARMED để khởi động Quadcopter chưa.

Nếu chưa, nhấn ARMED để khởi động 4 cánh quạt quay. Sau đó, xuất 1 tín hiệu để

Quadcopter cất cánh. Sau đó nhấn “H” để kích hoạt chế độ giữ độ cao cho Quadcopter.

Khi đó, cảm biến khoảng cách sẽ trả về giá trị khoảng cách từ Quadcopter đến mặt đất.

Giá trị này sẽ được tính toán sai số so với giá trị đặt, sau đó đưa vào bộ điều khiển PID

để tính toán bộ điều khiển giữ độ cao. Giá trị này sau đó sẽ được hiệu chỉnh về khoảng

giá trị từ 1400-1600 để gửi tín hiệu về mạch bay điều khiển Quadcopter. Sau đó, cập

nhật lại vị trí và kiểm tra xem có nhấn nút DISARMED không. Nếu không thì tiếp tục

phản hồi lại vị trí về để tính toán sai số và PID. Nếu có nhấn DISARMED, thì kết thúc

chương trình.
Tuy nhiên, khi Quadcopter giữ được độ cao, Quadcopter vẫn có hiện tượng bị trôi

theo chiều ngang hoặc chiều dọc. Chính vì vậy, bộ điều khiển vị trí được thiết kế để tính

toán và điều khiển Quadcopter giữ vị trí ban đầu. Các giá trị vị trí dịch chuyển sẽ được

tính từ vector độ dịch chuyển thông qua phương pháp Optical Flow. Ở đây, hệ thống

CHƯƠNG 4. THUẬT TOÁN ĐIỀU KHIỂN

BỘ MÔN ĐIỀU KHIỂN TỰ ĐỘNG | 50

xem như Camera trùng với gốc tọa độ của Quadcopter nên độ dịch chuyển của

Quadcopter cũng là độ dịch chuyển của Camera. Độ dịch chuyển này sẽ được đưa vào

bộ điều khiển PID và xuất ra tín hiệu điều khiển Roll và Pitch của Quadcopter. Cũng

như với giá trị tín hiệu Throttle, ta cũng phải tính toán hiệu chỉnh về khoảng từ 1400-

1600. Bởi vì hệ thống chỉ quan tâm đến độ dịch chuyển độ cao cũng như độ dịch chuyển

theo trục x và y nên sẽ không tác động điều khiển đến tín hiệu điều khiển góc Yaw. Ta

được bộ điều khiển PID ổn định vị trí như Hình 4.5.

Hình 4.5: Sơ đồ khối bộ điều khiển PID vị trí

Công thức bộ điều khiển PID vị trí được trình bày như sau:

0

0

() ()

()
()
x | dichchuyen | tamcamera
y | dichchuyen | tamcamera

t
x
x | px x | ix | x | dx

t
y
y | py y | iy | y | dy
e | x | x
e | y | y
de t PID | K e t | K e dt K
dt

de t
PID | K e t | K e dt K
dt
= | −
= | −
= | + | +
= | + | +

ò

ò

(1.45)

Trong đó:

+

T
vitri | x | y e | e e = é | ù
ë | û

là sai số độ dịch chuyển vị trí của tâm camera ban đầu và vị trí

mới.
+
x

e

là sai số giữa hoành độ vị trí tâm camera
tamcamera x

và hoành độ vị trí camera
mới
dichchuyen x
+
y

e

là sai số giữa tung độ vị trí tâm camera
tamcamera y

và tung độ vị trí camera mới

dichchuyen y
+
K
px

, Kix

, Kdx

lần lượt là hệ số tỉ lệ, hệ số tích phân và hệ số đạo hàm của bộ điều khiển ổn định vị trí theo phương x.

CHƯƠNG 4. THUẬT TOÁN ĐIỀU KHIỂN

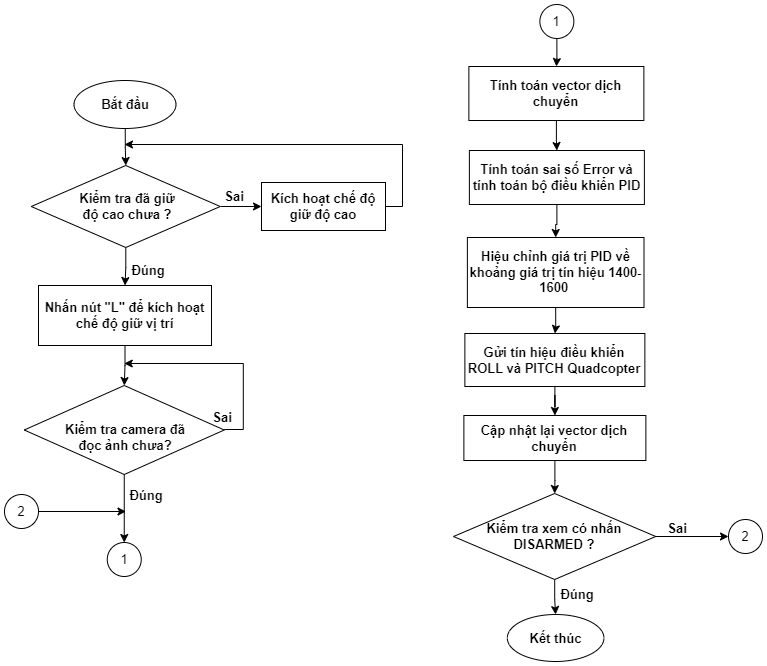
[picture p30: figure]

BỘ MÔN ĐIỀU KHIỂN TỰ ĐỘNG | 51

+
K
py

, Kiy

, Kdy

lần lượt là hệ số tỉ lệ, hệ số tích phân và hệ số đạo hàm của bộ

điều khiển ổn định vị trí theo phương y.

Lưu đồ trình bày quá trình vận hành bộ điều khiển vị trí được trình bày như

hình dưới đây:

Hình 4.6: Lưu đồ quá trình điều khiển vị trí Quadcopter

Ở thời điểm bắt đầu, kiểm tra đã Quadcopter đã ở trạng thái ổn định độ cao hay

chưa. Nếu chưa, kích hoạt chế độ giữ độ cao. Khi đã thấy Quadcopter ổn định được độ

cao, sau đó nhấn “L” để kích hoạt chế độ giữ vị trí cho Quadcopter. Khi này, kiểm tra

camera đã đọc ảnh chưa. Từ camera, áp dụng thuật toán Optical Flow để tính toán vector

dịch chuyển của vị trí mới so với tâm camera gốc. Giá trị này sẽ là sai số, sau đó đưa

vào bộ điều khiển PID để tính toán bộ điều khiển giữ vị trí. Giá trị này sau đó sẽ được

hiệu chỉnh về khoảng giá trị từ 1400-1600 để gửi tín hiệu về mạch bay điều khiển ROLL

và PITCH của Quadcopter. Sau đó, cập nhật lại vị trí mới và tính toán cập nhật lại vector dịch chuyển. Kế đó, kiểm tra xem có nhấn nút DISARMED không. Nếu không thì tiếp

CHƯƠNG 4. THUẬT TOÁN ĐIỀU KHIỂN

BỘ MÔN ĐIỀU KHIỂN TỰ ĐỘNG | 52

tục phản hồi lại vector dịch chuyển về để tính toán sai số và PID để điều khiển

Quadcopter. Nếu có nhấn DISARMED, thì kết thúc chương trình.

Kết hợp 2 bộ điều khiển độ cao Hình 4.3 và bộ điều khiển vị trí Hình 4.5, ta được

bộ điều khiển như Hình 4.7 dưới đây:

Hình 4.7: Bộ điều khiển chung của hệ thống

### 4.4 LƯU ĐỒ TỔNG QUAN HOẠT ĐỘNG CỦA DRONE

Lưu đồ này sẽ đưa ra chi tiết toàn bộ quá trình vận hành của hệ thống với mục tiêu

Quadcopter giữ được vị trí so với điểm ban đầu.

CHƯƠNG 4. THUẬT TOÁN ĐIỀU KHIỂN

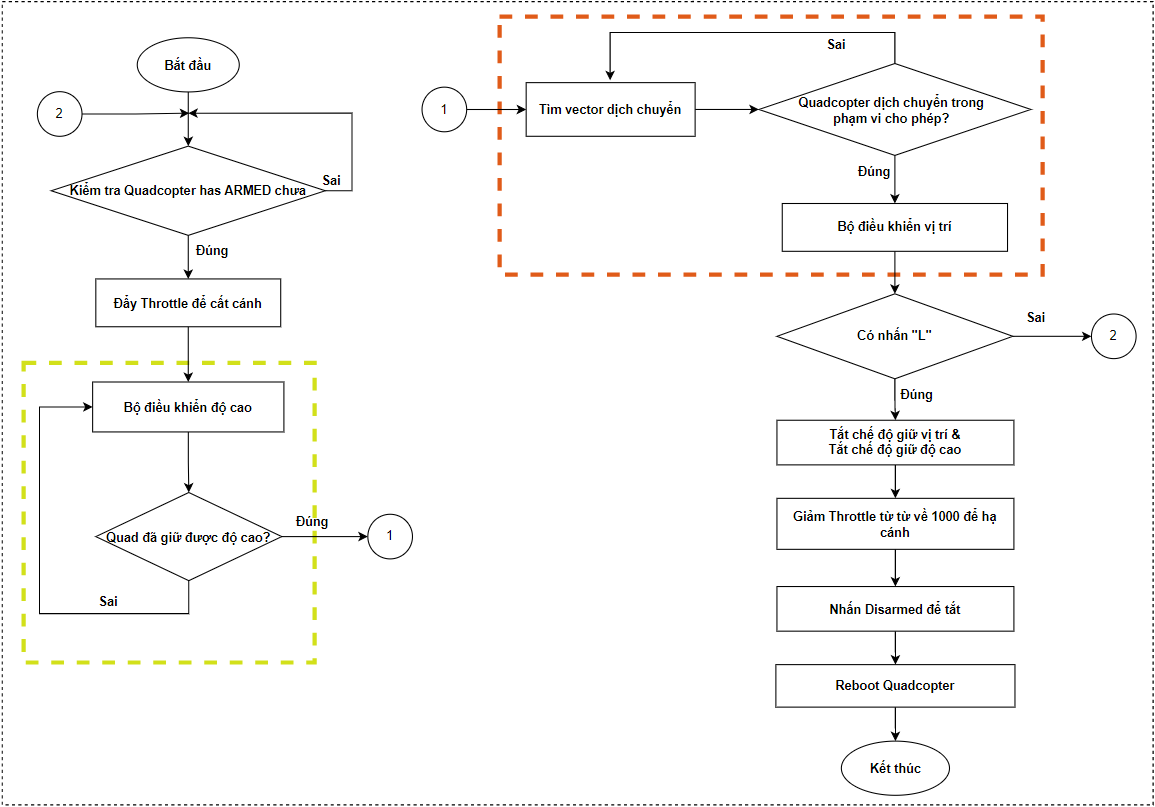
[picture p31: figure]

BỘ MÔN ĐIỀU KHIỂN TỰ ĐỘNG | 53

Hình 4.8: Lưu đồ hoạt động của Drone

Đầu tiên, Quadcopter sẽ kiểm tra trạng thái hoạt động của mình xem đã ở mode

ARM hay chưa. Nếu ARM đã bật, các cánh quạt sẽ bắt đầu quay nhưng chỉ là quay nhẹ

chưa đủ lực để nâng Quadcopter lên.

Kế đó, sẽ tiến hành nhấn nút để cất cánh cho Quadcopter bằng cách gửi một tín

hiệu Throttle lớn đến mạch điều khiển (tầm 1500). Khi này, Quadcopter sẽ đột ngột thay

đổi độ cao và khi bay sẽ có quán tính bay vọt lên.

Sau khi bay vọt quá độ cao tối thiểu mà đã cài đặt, thì sẽ bật chế độ giữ độ cao với

bộ PID độ cao điều chỉnh tín hiệu Throttle. Sau một thời gian, Quadcopter sẽ ổn định

dao động quanh vị trí đặt Setpoint.
Khi Quadcopter đã ổn định được độ cao, sẽ nhấn nút để kích hoạt camera vận hành

quá trình xử lý ảnh để tìm vector dịch chuyển. Sau một thời gian, Quadcopter sẽ dao

động quanh một điểm với độ dịch chuyển bé hơn 50cm. Sau khi thực hiện sau nhiệm

vụ, nhấn nút để giảm từ từ giá trị Throttle và nhấn Disarm để tắt Quadcopter.

Để làm rõ hơn, lưu đồ được đánh dấu các vùng thể hiện 2 luồng dữ liệu chính của

đề tài. Chi tiết hơn, ta có thể trình bày như sau:

CHƯƠNG 4. THUẬT TOÁN ĐIỀU KHIỂN

BỘ MÔN ĐIỀU KHIỂN TỰ ĐỘNG | 54

+ Với những đường nét đứt màu vàng, nó thể hiện bao hàm luồng điều khiển giữ

độ cao với tín hiệu vào là độ cao đọc từ cảm biến Lidar 1D và ngõ ra là tín hiệu điều

khiển Throttle nhằm giữ độ cao cho Quadcopter.

+ Với những đường nét đứt màu đỏ, nó thể hiện bao hàm luồng điều khiển giữ vị

trí với tín hiệu vào là độ dịch chuyển vector thông qua thuật toán Optical Flow và ngõ

ra là tín hiệu điều khiển Roll và Pitch nhằm điều khiển định hướng x và y cho

Quadcopter.

CHƯƠNG 5. KẾT QUẢ VÀ ĐÁNH GIẢ

BỘ MÔN ĐIỀU KHIỂN TỰ ĐỘNG | 55

## Chương 5. KẾT QUẢ VÀ ĐÁNH GIÁ

### 5.1 LỌC TÍN HIỆU CẢM BIẾN KHOẢNG CÁCH

Ở đề tài này, bộ lọc

αβ − Kalman đã được sử dụng để lọc nhiễu tín hiệu đầu vào

để đưa ra tín hiệu đầu ra đỡ bị nhiễu hơn. Dưới đây là kết quả khi so sánh dữ liệu chưa

lọc và đã qua bộ lọc Kalman.

Hình 5.1: Kết quả so sánh dữ liệu chưa lọc và đã qua bộ lọc Kalman

Dựa vào đồ thị trên, ta thấy với bộ lọc Kalman đã được sử dụng cho ra đường tín

hiệu (màu xanh) ít bị nhiễu hơn so với khi chưa có bộ lọc. Tuy nhiên, cảm biến Lidar

1D khá tốt nên sai số giữa tín hiệu chưa lọc và đã lọc là khá nhỏ.

### 5.2 ĐÁNH GIÁ THUẬT TOÁN XỬ LÝ ẢNH

### 5.2.1 Quá trình hiệu chỉnh Camera

Do camera luôn bị cong nên giá trị thuật toán xử lý ảnh thường bị sai. Chính vì vây, quá trình hiệu chỉnh Camera đóng vai trò rất quan trọng. Quá trình hiệu chỉnh

Camera được thể hiện ở Hình 5.2 dưới đây:

CHƯƠNG 5. KẾT QUẢ VÀ ĐÁNH GIẢ

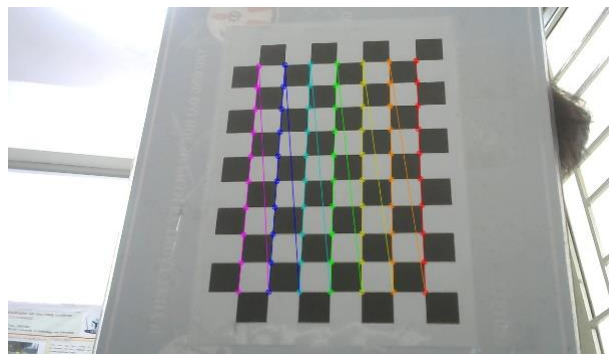
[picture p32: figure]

BỘ MÔN ĐIỀU KHIỂN TỰ ĐỘNG | 56

Hình 5.2: Quá trình hiệu chỉnh Camera

Sau khi hiệu chỉnh, ta sẽ tìm được thông số của ma trận camera, mà ở đó chúng ta

sẽ tìm được độ dài tiêu cự lần lượt là
Fx =1455.40

và

Fy =1446.54.

Sau đó, ta sẽ tính được độ dịch chuyển từ pixel sang đơn vị khác ví dụ như mét,

cen-ti-mét,.. bằng công thức dưới đây:

w
x
x

h
y
y

hI d
f
hI d
f

=

=

(1.46)

Trong đó,
w

I

là chiều dài của khung hình và dx

là chiều dài camera quan sát được

trong thực tế. Tương tự,
h

I

là chiều cao của khung hình và dy

là chiều cao camera quan

sát được trong thực tế.

### 5.2.2 Kết quả thuật toán Optical Flow

Sau đây, kết quả thuật toán Optical flow sẽ được trình bày trong hai trường hợp là

khi môi trường có ít đặc trưng và khi có nhiều đặc trưng:

CHƯƠNG 5. KẾT QUẢ VÀ ĐÁNH GIẢ

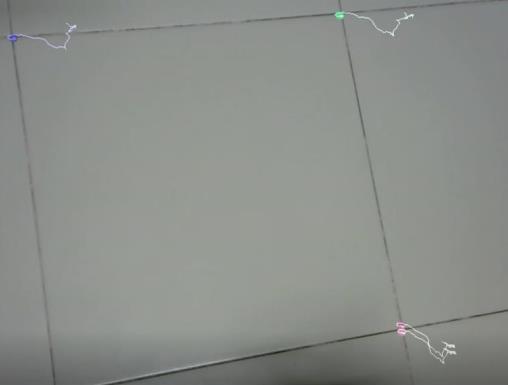
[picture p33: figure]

BỘ MÔN ĐIỀU KHIỂN TỰ ĐỘNG | 57

Hình 5.3: Kết quả áp dụng thuật toán PLK khi có ít đặc trưng

Hình 5.4: Kết quả áp dụng thuật toán PLK khi có nhiều đặc trưng

Ở Hình 5.3Error! Reference source not found., phương pháp Shi-Tomasi tìm

được rất ít đặc trưng tốt vì cường độ của các pixel trong khung hình có giá trị không

chênh lệch nhau nhiều. Tuy nhiên thuật toán PLK (Pyramid Lucas – Kanade) vẫn có thể

bám theo các đặc trưng này rất tốt. Ngược lại, Hình 5.4Error! Reference source not

found. có rất nhiều điểm pixel chênh lệch nhau rõ rệt về cường độ nên phương pháp

Shi-Tomasi tìm được rất nhiều đặc trưng tốt để PLK bám theo. Các nhiều đặc trưng

được trích xuất thì thông tin đưa về để tính toán độ dịch chuyển càng chính xác.

### 5.3 ĐÁNH GIÁ BỘ ĐIỀU KHIỂN PID

Bộ điều khiển PID áp dụng cho mô hình Drone để điều khiển giữ độ cao và vị trí.

Hình 5.5 ghi lại hình ảnh quadcopter giữ cân bằng và vị trí trong thực tế trong môi trường

ngoài trời.

CHƯƠNG 5. KẾT QUẢ VÀ ĐÁNH GIẢ

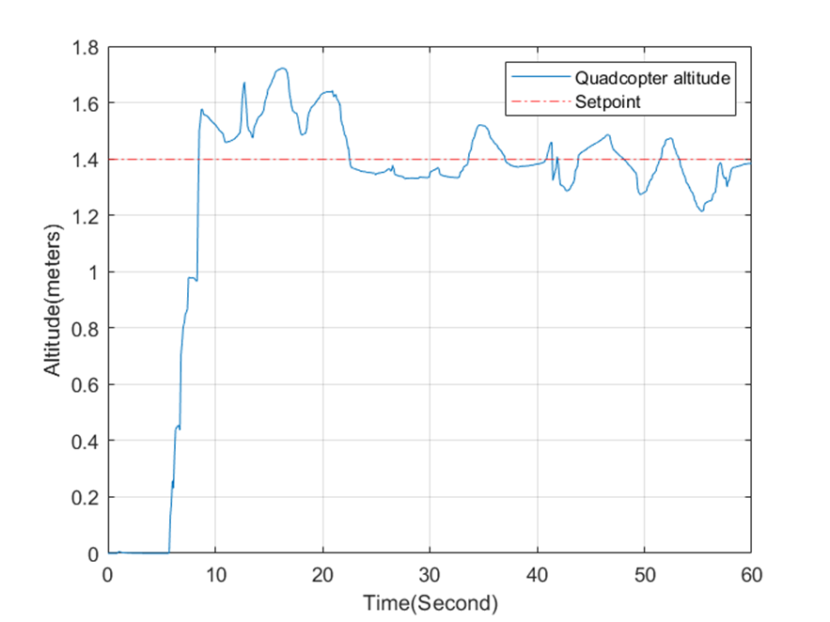
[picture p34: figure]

BỘ MÔN ĐIỀU KHIỂN TỰ ĐỘNG | 58

Hình 5.5: Kết quả thực tế quadcopter giữ độ cao và vị trí

Hình 5.6 thể hiện kết quả cho bộ điều khiển giữ ổn định độ cao. Theo ta nhìn thấy

từ đồ thị ban đầu khi độ cao bằng 0 là vị trí Quadcopter đang nằm dưới mặt đất. Khi

chúng ta kích một tín hiệu đẩy Throttle lên 1500 thì quadcopter cất cánh vọt lên độ cao

tầm khoảng 1.75m rồi bắt đầu điều chỉnh Throttle quanh vị trí setpoint là 1.4m.

Hình 5.6: Kết quả bộ điều khiển PID giữ độ cao

Đánh giá: Nhóm đã nêu phương pháp chọn khâu điều khiển và chọn ra các thông

số bộ điều khiển cho kết quả tốt nhất trong các lần thử sai. Các thông số này được áp

CHƯƠNG 5. KẾT QUẢ VÀ ĐÁNH GIẢ

BỘ MÔN ĐIỀU KHIỂN TỰ ĐỘNG | 59

dụng vào mô hình thực tế và cho kết quả không thật sự tốt. Tuy quadcopter vẫn giữ được

cân bằng nhưng quá trình cất cánh lên cao bị lệch và quadcopter còn rung lắc nhiều.

### 5.4 ĐÁNH GIÁ VỀ ĐỘ ỔN ĐỊNH CỦA QUADCOPTER

Hình 5.7 và Hình 5.8 dưới đây thể hiện góc Roll và góc Pitch khi bay trong thực tế.

Hình 5.7: Đồ thị thể hiện góc Roll khi bay trong thực tế

Ban đầu, khi chưa cất cánh, thì góc Roll của Quadcopter đọc về là 0.2⁰ khi để dưới

mặt đất. Khi cất cánh lên, góc Roll có sự thay đổi khi dao động trong tầm khoảng -2
0

đến 2⁰

. Độ lệch góc này khá nhỏ và trong tầm cho phép.

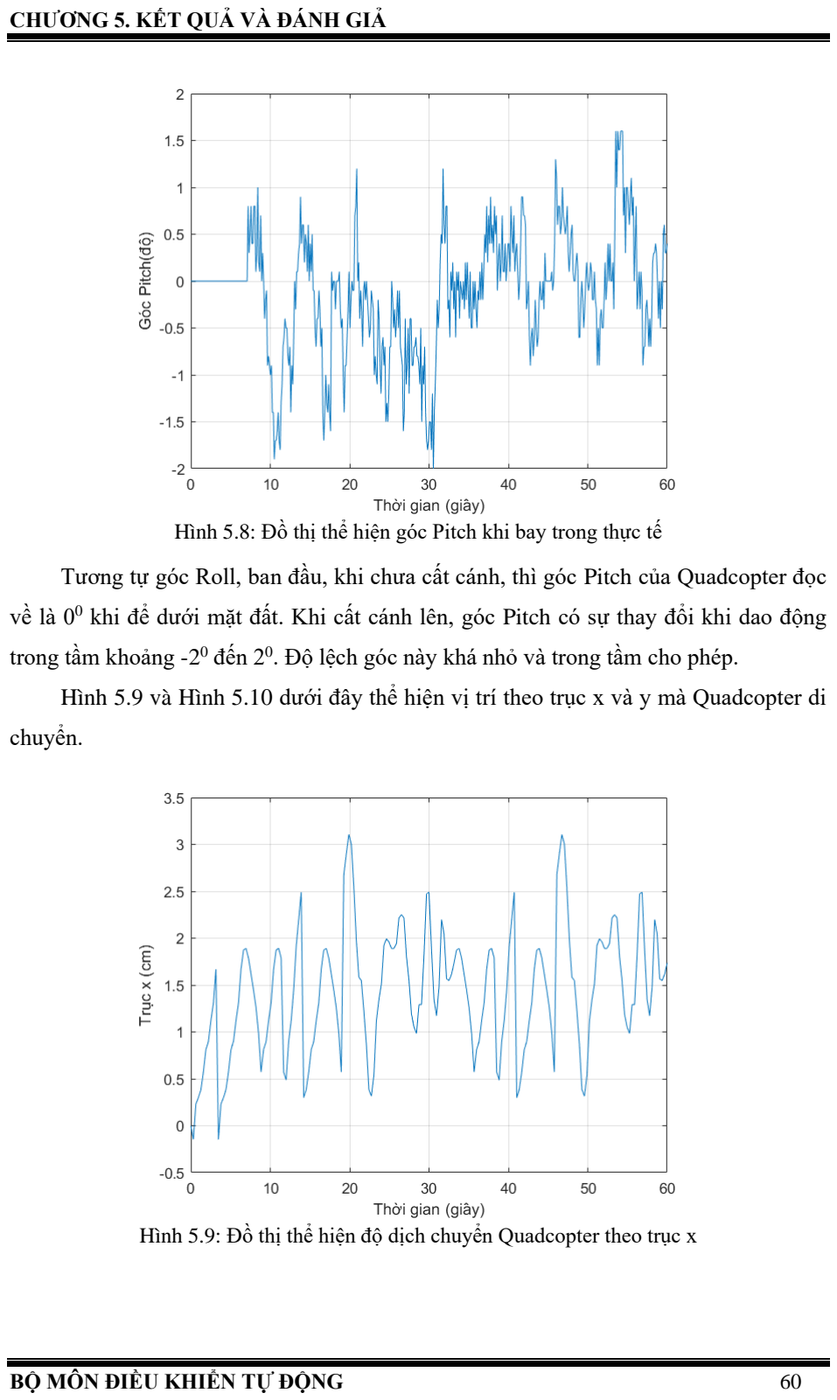
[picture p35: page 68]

CHƯƠNG 5. KẾT QUẢ VÀ ĐÁNH GIẢ

BỘ MÔN ĐIỀU KHIỂN TỰ ĐỘNG | 60

Hình 5.8: Đồ thị thể hiện góc Pitch khi bay trong thực tế

Tương tự góc Roll, ban đầu, khi chưa cất cánh, thì góc Pitch của Quadcopter đọc

về là 0⁰ khi để dưới mặt đất. Khi cất cánh lên, góc Pitch có sự thay đổi khi dao động

trong tầm khoảng -2

0 đến 2⁰

. Độ lệch góc này khá nhỏ và trong tầm cho phép.

Hình 5.9 và Hình 5.10 dưới đây thể hiện vị trí theo trục x và y mà Quadcopter di

chuyển.

Hình 5.9: Đồ thị thể hiện độ dịch chuyển Quadcopter theo trục x

CHƯƠNG 5. KẾT QUẢ VÀ ĐÁNH GIẢ

BỘ MÔN ĐIỀU KHIỂN TỰ ĐỘNG | 61

Hình 5.10: Đồ thị thể hiện độ dịch chuyển Quadcopter theo trục y

Kết quả cho thấy Quadcopter giữ vị trí khá tốt trong hệ tọa độ Oxy khi độ dịch

chuyển theo phương x và phương y là khá nhỏ (chỉ vài cm). Tuy nhiên, Quadcopter vẫn

bị trôi một đoạn so với gốc tọa độ, nhưng mà độ dịch chuyển không lớn, vẫn trong tầm

kiểm soát. Quadcopter ban đầu bị trôi một đoạn thì mới ổn định tại một vị trí cách tâm

một khoảng khá nhỏ.

### 5.5 KẾT LUẬN VÀ HƯỚNG PHÁT TRIỂN

### 5.5.1 Kết luận

Thông qua kết quả điều khiển thực nghiệm, nhóm đã áp dụng thành công phương

pháp Optical flow để đo đạc vị trí, vận tốc tuyến tính của quadcopter. Từ đó, thiết kế và

tinh chỉnh thành công thông số bộ điều khiển PID để điều khiển giữ ổn định và vị trí cho

quadcopter.

### 5.5.2 Hướng phát triển

Tuy hệ thống giữ ổn định khá tốt nhưng việc tìm kiếm và tinh chỉnh thông số bộ

điều khiển PID rất khó khăn và mất nhiều thời gian. Nhóm cũng nhận thấy hệ quadcopter

rất dễ bị ảnh hưởng bởi nhiễu bên ngoài như gió. Bên cạnh đó, PID là một bộ điều khiển

tuyến tính nên cũng còn nhiều hạn chế. Do đó, nhóm đề xuất sử dụng các bộ điều khiển

phi tuyến hoặc thích nghi có thể điều khiển hệ thống dưới tình trạng nhiễu này hoặc sử

dụng học củng cố để huấn luyện và điều khiển thực tế cho hệ quadcopter.

TÀI LIỆU THAM KHẢO

62

## TÀI LIỆU THAM KHẢO

[1] E. Kuantama, T. Vesselenyi, S. Dzitac, and R. Tarca, “PID and Fuzzy-PID control model for quadcopter attitude with disturbance parameter,” Int. J. Comput. Commun. Control, vol. 12, no. 4, pp. 519–532, 2017, doi: 10.15837/ijccc.2017.4.2962.
[2] Ngoc-Hien-Duc Le, Thuy-Huynh Duong, Huy-Phuong Le, Tran-Nhat-Minh Ta and My-Ha Le, “ Autonomous Landing of a Quadcopter on a Stationary Platform,” International Conference on System Science and Engineering, Nha Trang,2021, Place of Publication: Xplore Proceedings of ICSSE 2021,2021, paper ID : 18.
[3] Manh. Cuong. Le and My. Ha. Le, “Human Detection and Tracking for Autonomous Human-following Quadcopter,” Proc. 2019 Int. Conf. Syst. Sci. Eng. ICSSE 2019, pp. 6–11, 2019, doi: 10.1109/ICSSE.2019.8823343.
[4] E. Kuantama, I. Tarca, and R. Tarca, “Quadcopter Modeling in Virtual Reality for Dynamic Visualization,” 2018 5th Int. Conf. Control. Decis. Inf. Technol. CoDIT 2018, pp. 671–676, 2018, doi: 10.1109/CoDIT.2018.8394860.
[5] R. P. Borase, D. K. Maghade, S. Y. Sondkar, and S. N. Pawar, “A review of PID control, tuning methods and applications,” International Journal of Dynamics and Control. Springer, 2020, doi: 10.1007/s40435-020-00665-4.
[6] Omar Daniel Mora Granillo, Zizilia Zamudio Beltrán. “Real-Time Drone (UAV) Trajectory Generation and Tracking by Optical Flow”. International Conference on Mechatronics, Electronics and Automotive Engineering, 2018.

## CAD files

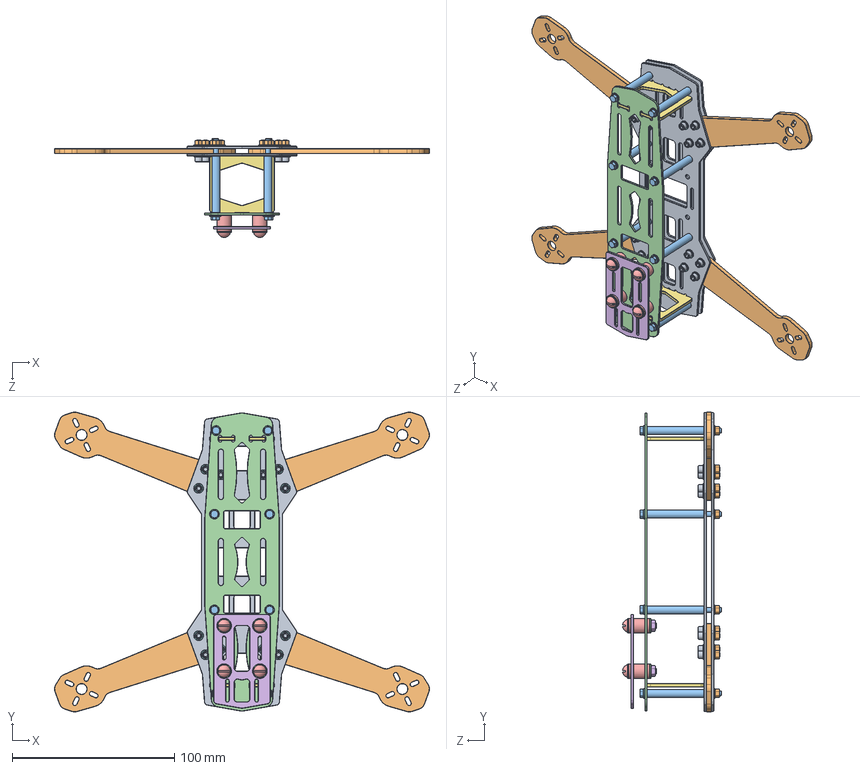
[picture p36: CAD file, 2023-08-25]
Solidworks/File Solidworks/ZMR250 Quadcopter Frame _Assembly.SLDASM
231.1 x 184.9 x 61.0 mm
Bottom Plate.ipt x 2
Arm.ipt x 4
Spacer.ipt x 8
Top Plate.ipt
Damper.ipt x 4
Camera Plate.ipt
FPV Plate.ipt x 2
Lock Washer.ipt x 48
Hex Socket Screw.ipt x 16
Hex Nut with Washer Face.ipt x 24
Hex Head Cap Screw.ipt x 8
Lock Washer -2.ipt x 8
Round Head Machine Screw.ipt x 4
Hex Jam Nut with Washer Face.ipt x 4

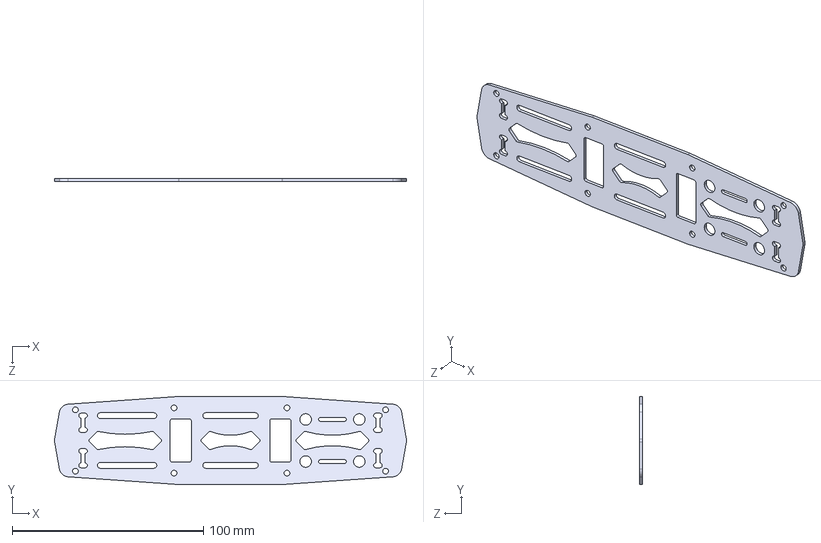
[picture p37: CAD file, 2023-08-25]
Solidworks/File Solidworks/TopPlate.STEP
183.8 x 46.0 x 1.50 mm

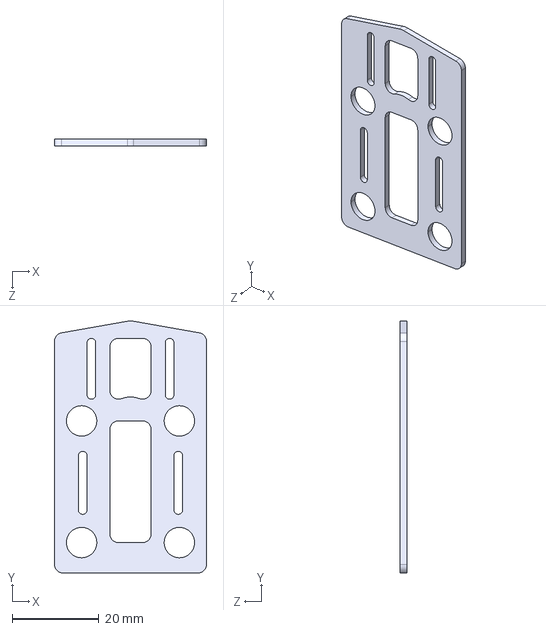
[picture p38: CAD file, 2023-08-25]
Solidworks/File Solidworks/CameraPlate.STEP
35.0 x 58.0 x 1.50 mm

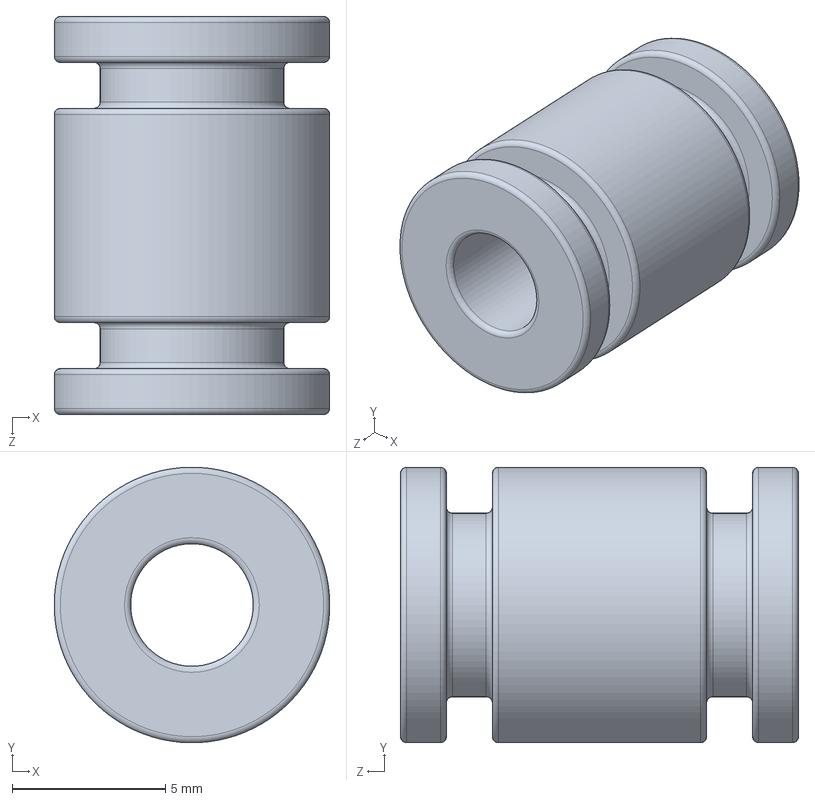
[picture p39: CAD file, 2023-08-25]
Solidworks/File Solidworks/DAMPER1.SLDPRT
9.00 x 9.00 x 13.0 mm

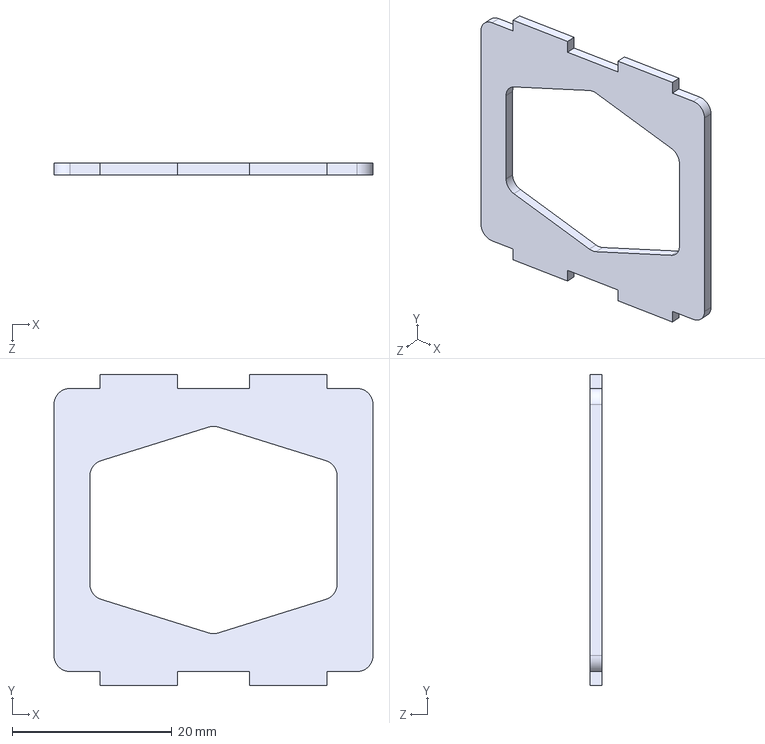
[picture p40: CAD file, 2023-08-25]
Solidworks/File Solidworks/FPVPlate.STEP
40.0 x 39.0 x 1.50 mm

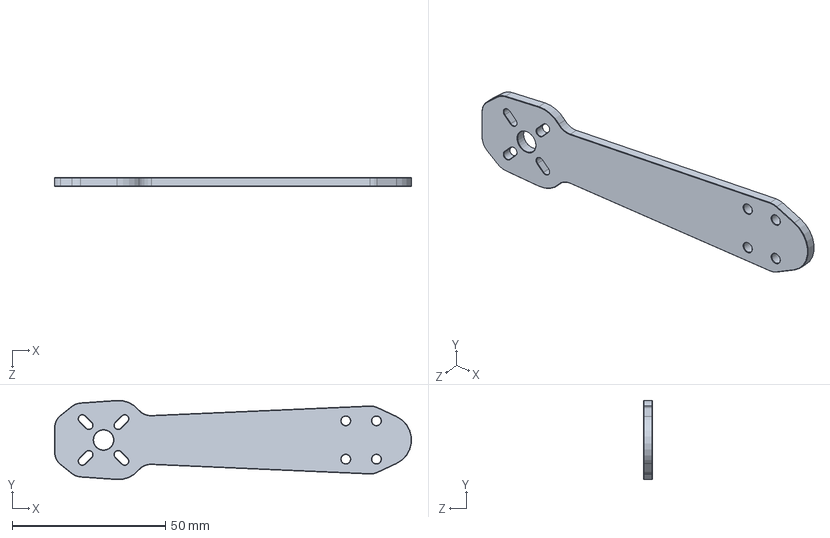
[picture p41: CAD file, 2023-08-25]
Solidworks/File Solidworks/Arm_2.SLDPRT
116.4 x 25.9 x 3.00 mm

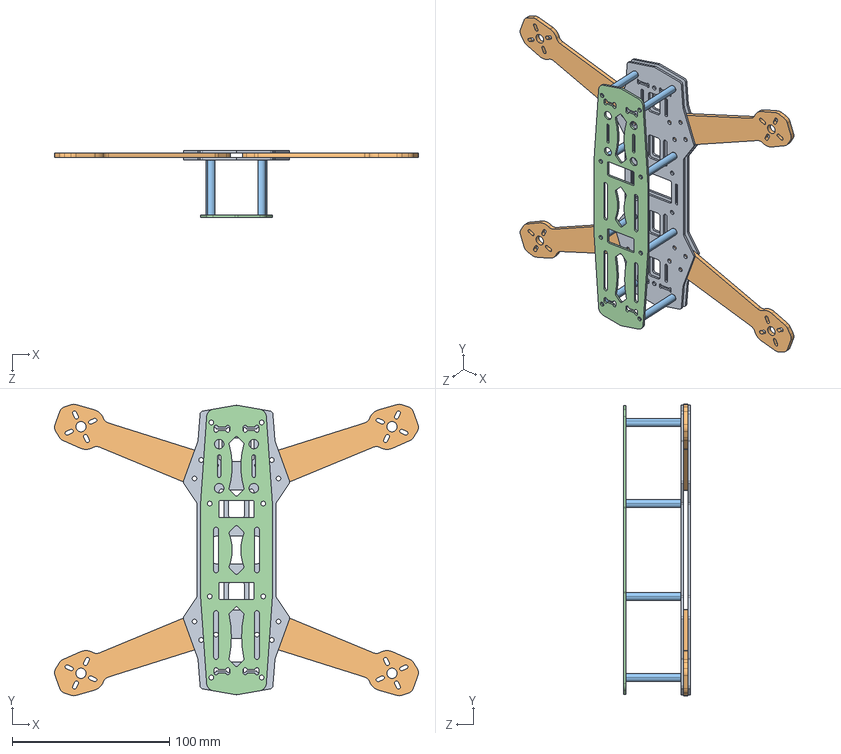
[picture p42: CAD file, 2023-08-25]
Solidworks/File Solidworks/Rahmen.STEP
231.2 x 185.2 x 42.5 mm
BottomPlate x 2
Arm x 4
Spacer x 8
TopPlate

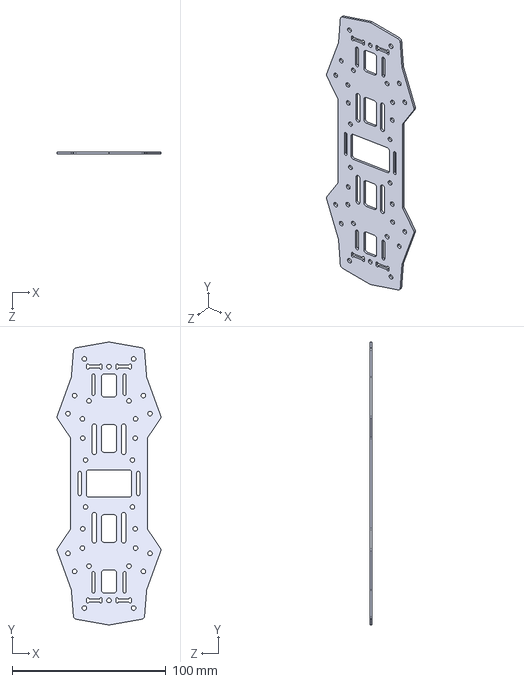
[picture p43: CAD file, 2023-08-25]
Solidworks/File Solidworks/BottomPlate.STEP
67.5 x 184.0 x 1.50 mm

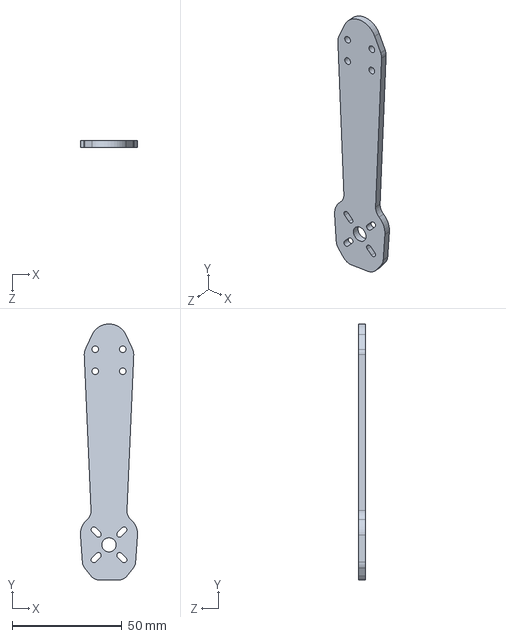
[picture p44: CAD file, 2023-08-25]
Solidworks/File Solidworks/Part3.SLDPRT
26.0 x 116.5 x 3.00 mm

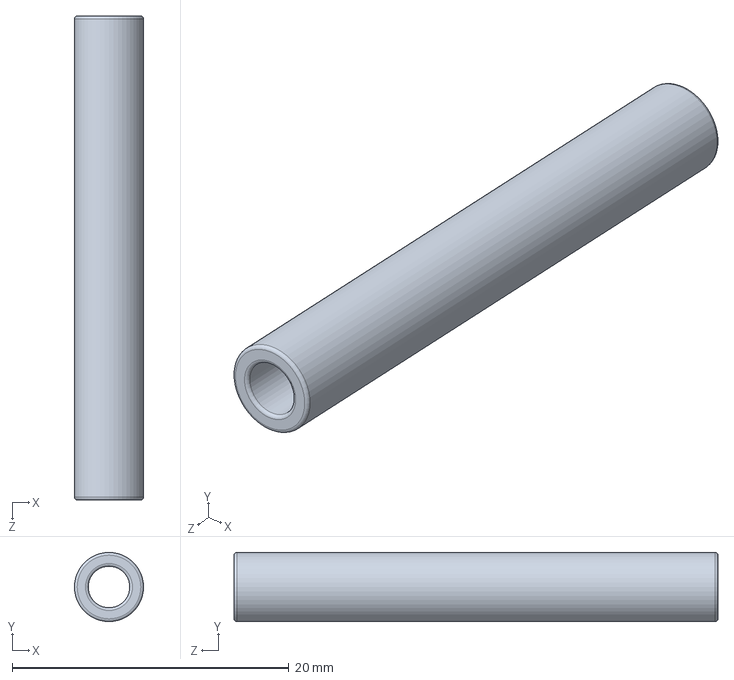
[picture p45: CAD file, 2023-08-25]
Solidworks/File Solidworks/Spacer1.SLDPRT
5.00 x 5.00 x 35.0 mm

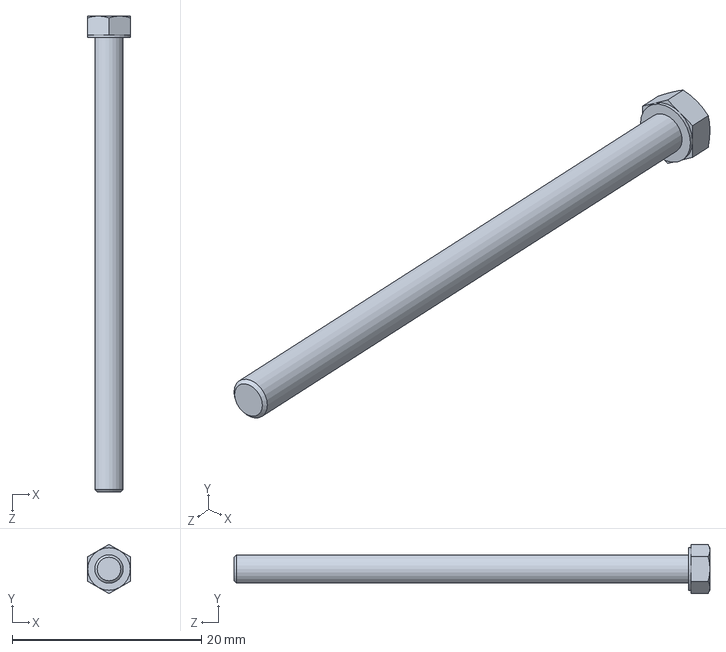
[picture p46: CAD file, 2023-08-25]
Solidworks/File Solidworks/Hex Head Cap Screw.SLDPRT
4.50 x 5.20 x 50.3 mm

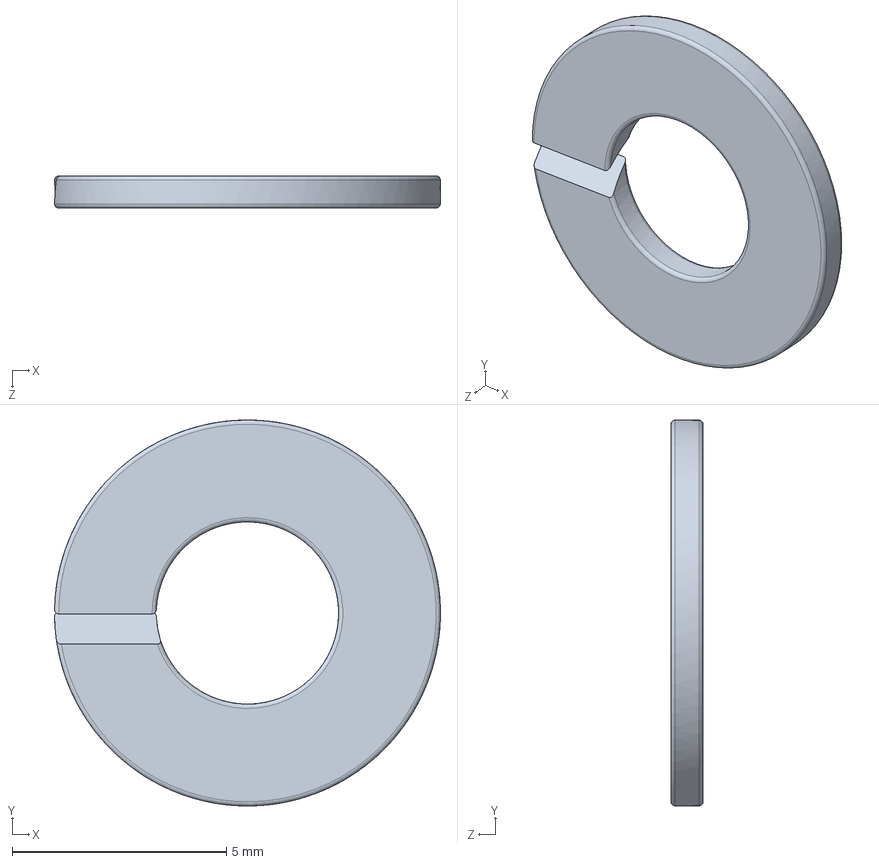
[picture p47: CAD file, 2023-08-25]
Solidworks/File Solidworks/Lock Washer -2.SLDPRT
9.00 x 9.00 x 0.75 mm

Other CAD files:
Solidworks/File Solidworks/Arm_1.sldprt
Solidworks/File Solidworks/Part6.SLDPRT
Solidworks/File Solidworks/Damper.STEP
Solidworks/File Solidworks/Spacer.STEP
Solidworks/File Solidworks/Arm.STEP
Solidworks/File Solidworks/BottomPlate_1.sldprt
Solidworks/File Solidworks/Arm.SLDPRT
Solidworks/File Solidworks/Arm.ipt
Solidworks/File Solidworks/Bottom Plate.ipt
Solidworks/File Solidworks/BottomPlate.SLDPRT
Solidworks/File Solidworks/Camera Plate.ipt
Solidworks/File Solidworks/CameraPlate.SLDPRT
Solidworks/File Solidworks/DXF/Arm.dxf
Solidworks/File Solidworks/DXF/BottomPlate.dxf
Solidworks/File Solidworks/DXF/CameraPlate.dxf
Solidworks/File Solidworks/DXF/TopPlate.dxf
Solidworks/File Solidworks/Damper.ipt
Solidworks/File Solidworks/FPV Plate.ipt
Solidworks/File Solidworks/FPVPlate.SLDPRT
Solidworks/File Solidworks/Hex Head Cap Screw.ipt
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

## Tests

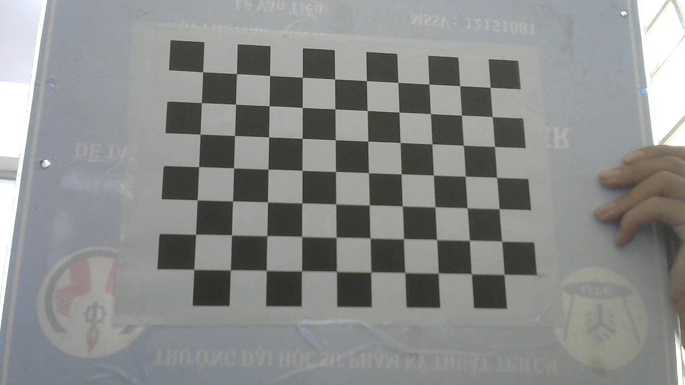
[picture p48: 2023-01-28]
src/calibration_camera/test_data/test_data4.png

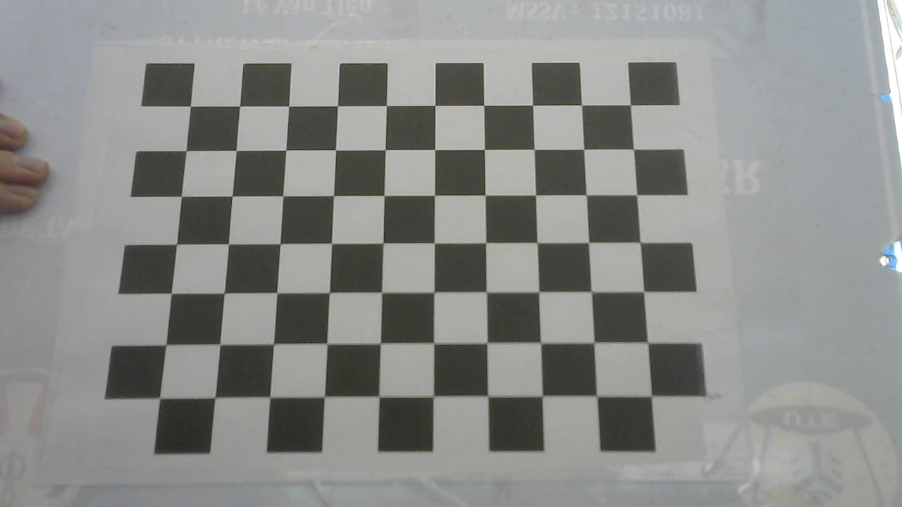
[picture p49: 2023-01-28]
src/calibration_camera/calib_data/data15.png

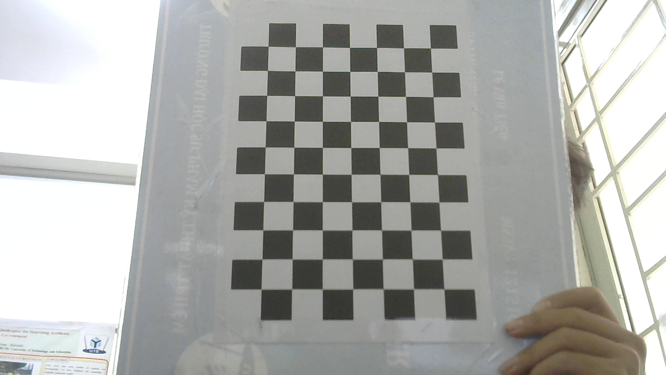
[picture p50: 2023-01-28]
src/calibration_camera/test_data/test_data6.png

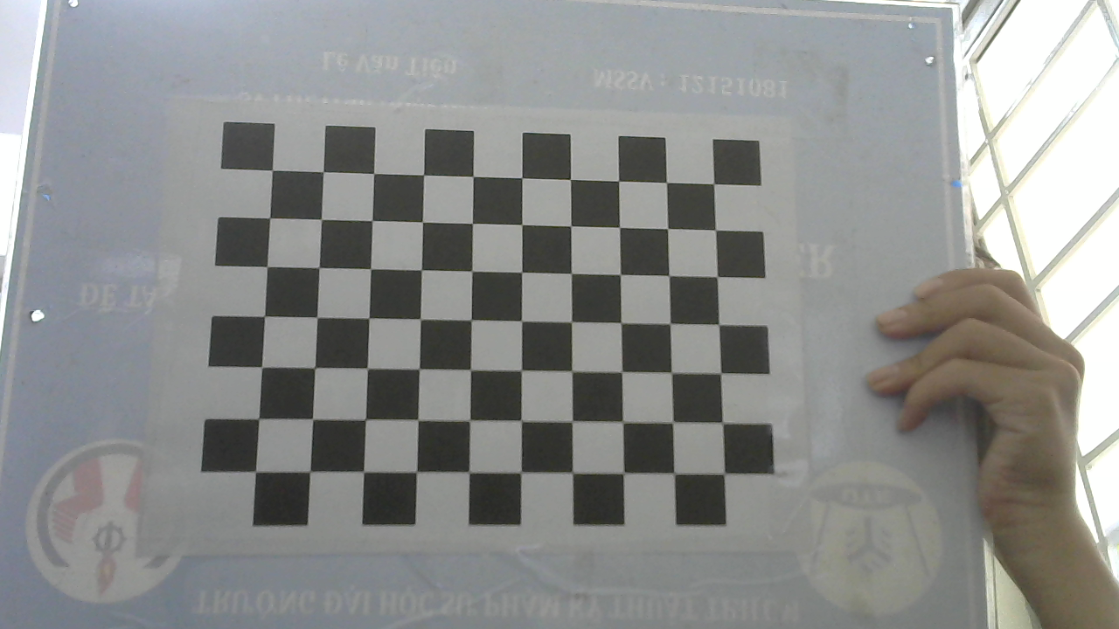
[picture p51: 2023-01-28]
src/calibration_camera/test_data/test_data1.png

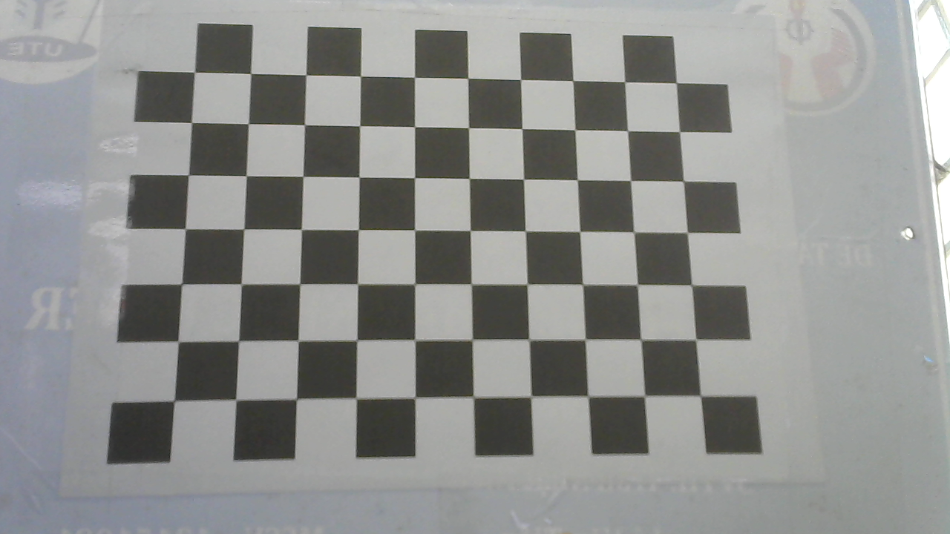
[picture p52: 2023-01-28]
src/calibration_camera/calib_data/data3.png

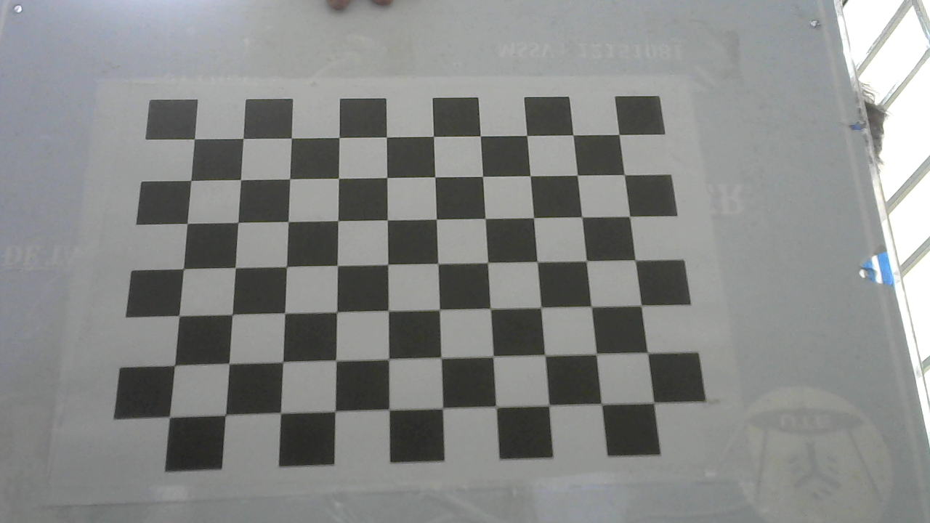
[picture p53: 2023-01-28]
src/calibration_camera/calib_data/data12.png

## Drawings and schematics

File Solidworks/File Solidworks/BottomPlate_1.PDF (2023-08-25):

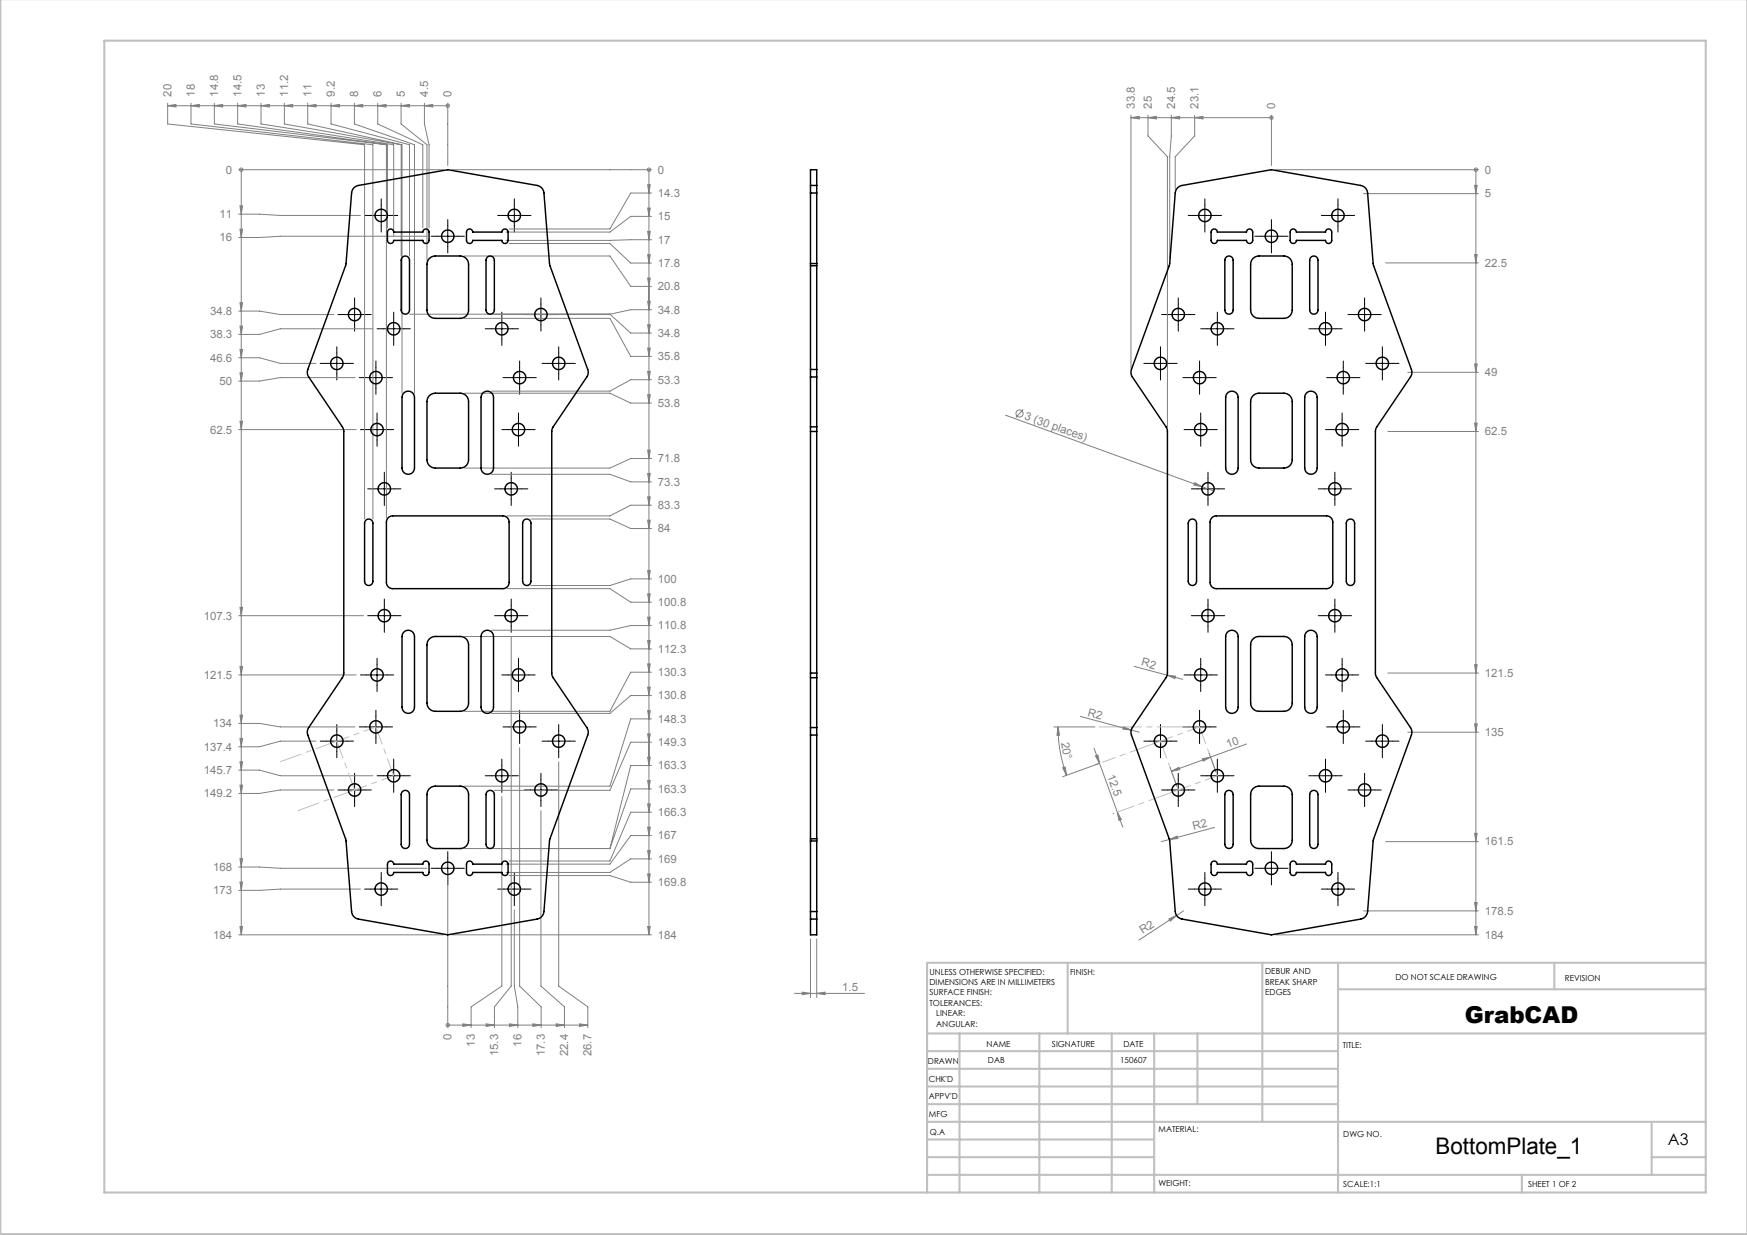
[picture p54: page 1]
3 (30 places); SCALE:1:1; SHEET 1 OF 2; DO NOT SCALE DRAWING; REVISION; DEBUR AND BREAK SHARP; UNLESS OTHERWISE SPECIFIED:; FINISH:

DIMENSIONS ARE IN MILLIMETERS
SURFACE FINISH:
TOLERANCES:
LINEAR:
ANGULAR:

NAME | SIGNATURE | DATE | | | | TITLE:

DRAWN | DAB | | 150607
CHK'D
APPV'D
MFG
Q.A | | | | MATERIAL: | DWG NO. BottomPlate_1 | A3

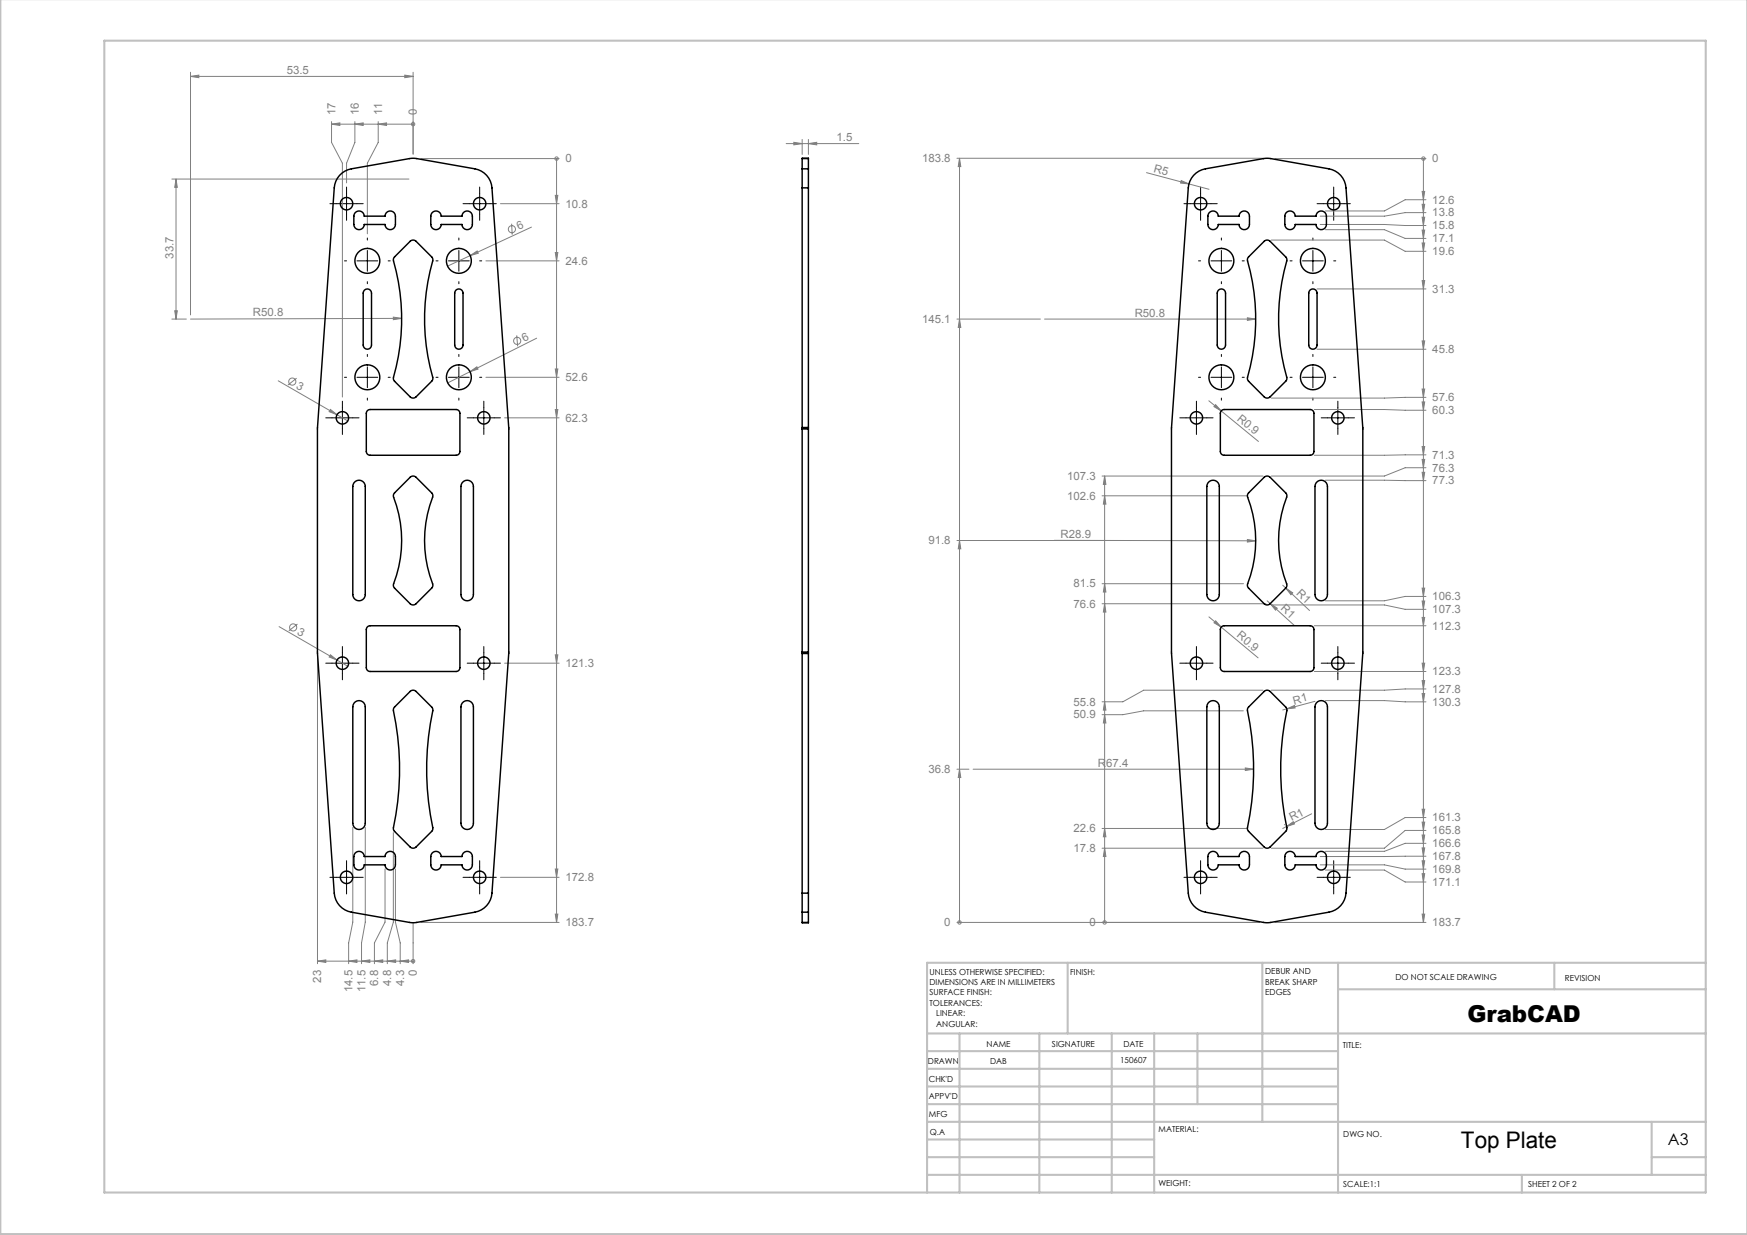
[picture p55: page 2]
SCALE:1:1; SHEET 2 OF 2; DO NOT SCALE DRAWING; REVISION; DEBUR AND BREAK SHARP; UNLESS OTHERWISE SPECIFIED:; FINISH:

DIMENSIONS ARE IN MILLIMETERS
SURFACE FINISH:
TOLERANCES:
LINEAR:
ANGULAR:

NAME | SIGNATURE | DATE | | | | TITLE:

DRAWN | DAB | | 150607
CHK'D
APPV'D
MFG
Q.A | | | | MATERIAL: | DWG NO. Top Plate | A3

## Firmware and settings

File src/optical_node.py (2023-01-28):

import numpy as np
import cv2
import time
import imutils
from imutils.video import WebcamVideoStream
from threading import Thread
from functools import reduce 


FC = [1455.40, 1446.54]  # focal lengths for GoPro Hero3+ Black
CC = [637.53, 316.53]  # principle points for same
KC = [0.03, 0.21, 0.00, -0.00, 0.46]  # distortion coeffs for same
fx, fy = FC
cx, cy = CC
cam_matrix = np.array([[fx,  0, cx],
                       [ 0, fy, cy],
                       [ 0,  0,  1]], dtype='float32')
distortion_profile = np.array(KC, dtype='float32')
class Optical(Thread):
    def __init__(self):
        #init thread
        Thread.__init__(self)
        #the for each point tracked, the location of that point in the previous 10 frames is stored
        self.trajectory_len = 10
        # a new set of points is detected very n frames
        self.detect_interval = 5
        self.trajectories = []
        self.frame_idx = 0
        # inital fps will be recalculated after self.fps_interval frames
        self.height = 1.5

        # a new fps is calculated every n frames
        self.fps_interval = 5
        # list of velocities relating to movement of points frame to frame
        self.vlist = []
        self.x = 0
        self.y = 0
        self.current_roll = 0
        self.current_pitch = 0
        self.lk_params = dict(winSize  = (25, 25),
                maxLevel = 1,
                criteria = (cv2.TERM_CRITERIA_EPS | cv2.TERM_CRITERIA_COUNT, 10, 0.03))

        self.feature_params = dict(maxCorners = 15,
                    qualityLevel = 0.3,
                    minDistance = 10,
                    blockSize = 7 )
        self.px = 0
        self.py = 0
        self.ROLL_DRIFT_SUM = 0
        self.PITCH_DRIFT_SUM = 0

    def run(self):
        #cap = WebcamVideoStream(src = 0).start()
        cap = cv2.VideoCapture('imageprocess.mp4')
        #fourcc = cv2.VideoWriter_fourcc('m', 'p', '4', 'v')
        #out = cv2.VideoWriter('output.mp4', fourcc, 25, (640, 480), isColor=True)
        fps = 30
        
        #f = open("optical1.txt","a")
        #t1 = time.time()

        pitch_drifts = []
        roll_drifts = []
        width = 960
        height = 564
        dsize = (width, height)

        while True:

    # start time to calculate FPS
    #start = time.time()

            ret, frame = cap.read()
            frame = cv2.resize(frame, dsize)
            frame_undisorted = cv2.undistort(frame, cam_matrix, distortion_profile)
            
            frame_gray = cv2.cvtColor(frame_undisorted, cv2.COLOR_BGR2GRAY)
            FrameW, FrameH = frame_gray.shape
            img = frame_undisorted.copy()

            # Calculate optical flow for a sparse feature set using the iterative Lucas-Kanade Method
            if len(self.trajectories) > 0:
                img0, img1 = self.prev_gray, frame_gray
                p0 = np.float32([trajectory[-1] for trajectory in self.trajectories]).reshape(-1, 1, 2)
                p1, _st, _err = cv2.calcOpticalFlowPyrLK(img0, img1, p0, None, **self.lk_params)
                NoKPts = 0
                if p1 is not None:
                    X_avg = 0
                    Y_avg = 0
                p0r, _st, _err = cv2.calcOpticalFlowPyrLK(img1, img0, p1, None, **self.lk_params)
                d = abs(p0-p0r).reshape(-1, 2).max(-1)
                good = d < 1

                new_trajectories = []
                for  trajectory, (x, y), good_flag in zip(self.trajectories, p1.reshape(-1, 2), good):
                    if not good_flag:
                        continue
                    trajectory.append((x, y))
                    if len(trajectory) > self.trajectory_len:
                        del trajectory[0]
                    new_trajectories.append(trajectory)
                    # Newest detected point
                    cv2.circle(img, (int(x), int(y)), 4, (50, 125, 255), -1)

                self.trajectories = new_trajectories
                #calculate velocity
                for tr in self.trajectories:
                    distances = []
                    prev_x , prev_y = tr[0][0], tr[0][1]
                    # for every position for a given point get the distance between
                    # two consecutive points, average that distance and calculate the
                    # speed in pxls/s
                    for i in range(len(tr)):
                        curr_x, curr_y = tr[i][0], tr[i][1]
                        self.x =curr_x-prev_x
                        self.y = curr_y-prev_y
                        prev_x, prev_y = curr_x, curr_y
                        #self.px = self.height/(float(fx)*(self.x-cx))
                        #self.py = self.height/(float(fy)*(self.y-cy))




                    # if the distance between two points is less than 1 pixel, ignore it
                    if abs(self.x) < 1.0 and abs(self.y) < 1.0:
                        continue
                    distances.append([self.x,self.y])
                    roll_drifts.append(self.px)
                    pitch_drifts.append(self.py)
                total = [0,0]
                # sum up all the distances for a given point
                for distance in distances:
                    total[0] += distance[0] # displacment x
                    total[1] += distance[1] #displacement y
                    NoKPts += 1
                



                # get the average of the summed points and calculate velocity of that
                #if len(distances) != 0:
                    #avg_distance = [total[0]/(len(distances)), total[1]/(len(distances))]
                    #v = [avg_distance[0]*fps, avg_distance[1]*fps]
                    #cv2.putText(img,, (20, 50), cv2.FONT_HERSHEY_PLAIN, 1, (0,255,0), 2)
                    #print("velocity is : ", v)

                    #self.vlist.append(v)
                # Draw all the trajectories
                cv2.polylines(img, [np.int32(trajectory) for trajectory in self.trajectories], False, (0, 255, 150))
                #cv2.putText(img, 'track count: %d' % len(self.trajectories), (20, 50), cv2.FONT_HERSHEY_PLAIN, 1, (0,255,0), 2)



            # Update interval - When to update and detect new features
            if self.frame_idx % self.detect_interval == 0:

                mask = np.zeros_like(frame_gray)
                del self.vlist[:]
                mask[:] = 255

                # Lastest point in latest trajectory
                for x, y in [np.int32(trajectory[-1]) for trajectory in self.trajectories]:
                    cv2.circle(mask, (x, y), 5, 0, -1)

                # Detect the good features to track
                p = cv2.goodFeaturesToTrack(frame_gray, mask = mask, **self.feature_params)
                
                if p is not None:
                    # If good features can be tracked - add that to the trajectories
                    for x, y in np.float32(p).reshape(-1, 2):
                        self.trajectories.append([(x, y)])
                        #cv2.putText(img, 'point count: %d' % len(p), (20, 80), cv2.FONT_HERSHEY_PLAIN, 1, (0,255,0), 2)


            self.frame_idx += 1
            self.prev_gray = frame_gray

            # calculate the FPS for current frame detection
            #fps = 1 / (end-start)
            
            # Show Results
            cv2.putText(img, f"{fps:.2f} FPS", (20, 30), cv2.FONT_HERSHEY_SIMPLEX, 1, (0, 255, 0), 2)
            cv2.imshow('Optical Flow', img)
            #out.write(img)
            #print("velocity shape is: ")
                        # press escape to exit the program
            ch = 0xFF & cv2.waitKey(1)
            if cv2.waitKey(10) & 0xFF == ord('q'):
                #print("velocity: " + str(self.vlist))
                cv2.destroyAllWindows()
                cap.stop()
                #out.release()
                break
if __name__ == '__main__':
    try:
        optical_thread = Optical()
        optical_thread.start()
    except:
        print("error")







        

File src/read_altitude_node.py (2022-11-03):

import serial
import time
from threading import Thread
class read_altitude(Thread):
    #This class is going to feedback the altitude captured by tof sensor
    def __init__(self):
        #create pipe
        #super(read_altitude(), self).__init__()
        #create serial read
        Thread.__init__(self)
        self.ser = serial.Serial("/dev/serial0", 115200,timeout=0) # mini UART serial device
        
    def getTFminiData(self):
        while True:
            count = self.ser.in_waiting
            if count > 8:
                recv = self.ser.read(9)
                self.ser.reset_input_buffer()
                if recv[0] == 0x59 and recv[1] == 0x59:
                    distance = recv[2] + recv[3] * 256
                    distance_meter = distance/100
                    print('The distance is: ',distance_meter)
                    self.ser.reset_input_buffer()
                #self.pipe_write.recv()     
    def run(self):
        try:
            if self.ser.is_open == False:
                self.ser.open()
            self.getTFminiData()
        except KeyboardInterrupt:
            if self.ser != None:
                self.ser.close()
if __name__ == '__main__':
    try:
        altitude_thread = read_altitude()
        altitude_thread.start()
    except:
        print("error")






        
